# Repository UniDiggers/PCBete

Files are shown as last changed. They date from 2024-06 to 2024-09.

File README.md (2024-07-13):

# PCBete

Création d'un PCB pour la robotique.

## Objectif :

Carte électronique ESP32-S3-WROOM-U1 permettant de controller : 
- Jusqu'à 3 NEMA 17 
- 3 Capteurs TOF VL53L0X (i2c)
- 1 écran OLED 0.96 128*64 (i2c) 
- Buzzer
- LiDAR*

Alimentation via PowerBank 5Ah avec 5V/3A vers la carte en Type-C vers Type-C .

## Consommation théorique 

**3000mA** sont disponibles :

- 1x ESP32 environ **150mA**
- 3x NEMA 17 environ **2400mA**
- 3x TOF VL53L0X environ **60mA**
- 1x Ecran OLED environ **15mA**
- 1x Buzzer environ **10mA**

**TOTAL THEORIQUE : 2635mA / 87%**
*Ce calcul ne prend pas en compte la consommation théorique des composants soudés à la carte.

*le LiDAR est un accessoire optionnel qui peut être ajouté si la consommation instantanée le permet.
1x LiDAR environ **150mA**.

TOTAL THEORIQUE avec LiDAR : **2785mA / 92%**

## Temps d'utilisation théorique

Energie Batterie = Capacité (Ah) x Tension sortie ( Volt).
Energie Batterie = 5Ah x 5 = **25Wh**.

Puissance carte = Intensité (A) x Tension (Volt).
Puissance carte = 3A x 5V = **15W**.

Temps d'utilisation (heure) = Energie Batterie (watt-heures) / Puissance carte (W).
Temps d'utilisation (heure) = 25Wh / 15W = **1.67 heures**.

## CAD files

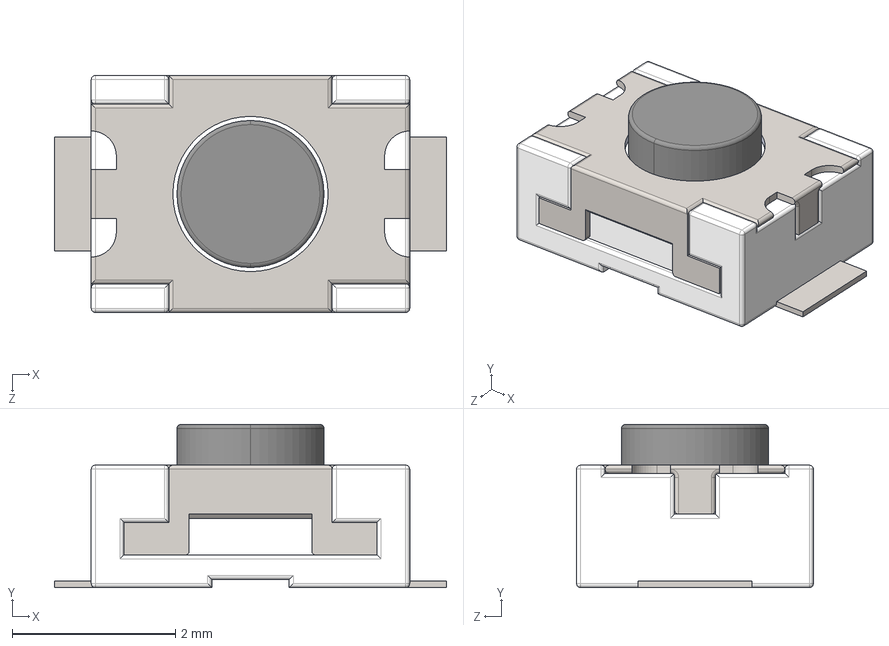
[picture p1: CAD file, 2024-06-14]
3D/Bouton/SKRKAEE020.stp
4.80 x 2.00 x 2.90 mm

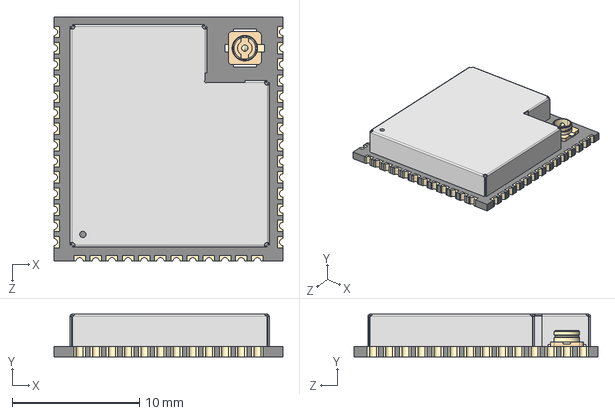
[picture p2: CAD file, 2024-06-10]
3D/ESP32-S3-WROOM-1U/ESP32-S3-WROOM-1U--3DModel-STEP-56544.STEP
18.0 x 3.35 x 19.2 mm

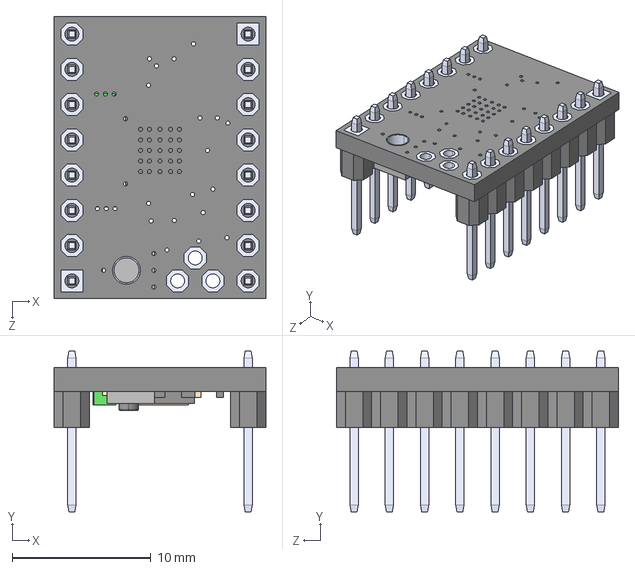
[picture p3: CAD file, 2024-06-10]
3D/TMC2209/TMC2209_SILENTSTEPSTICK.step
15.2 x 11.6 x 20.3 mm

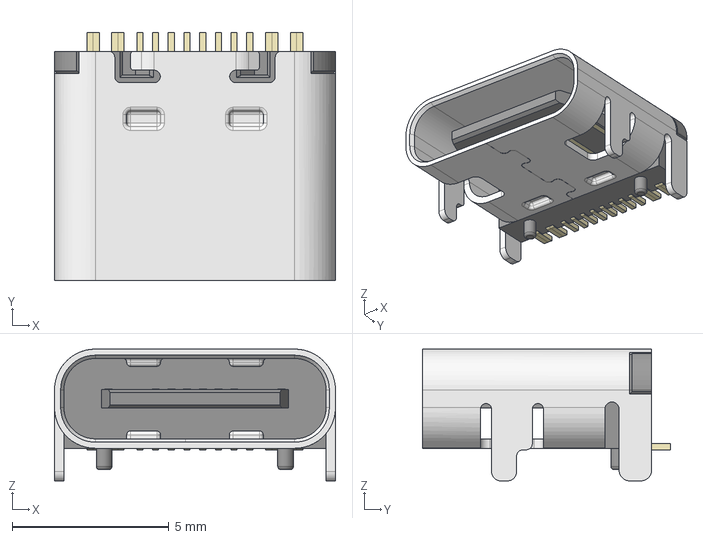
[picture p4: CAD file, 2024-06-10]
3D/USB-Type-C/HRO_TYPE-C-31-M-12.step
8.95 x 7.90 x 4.20 mm

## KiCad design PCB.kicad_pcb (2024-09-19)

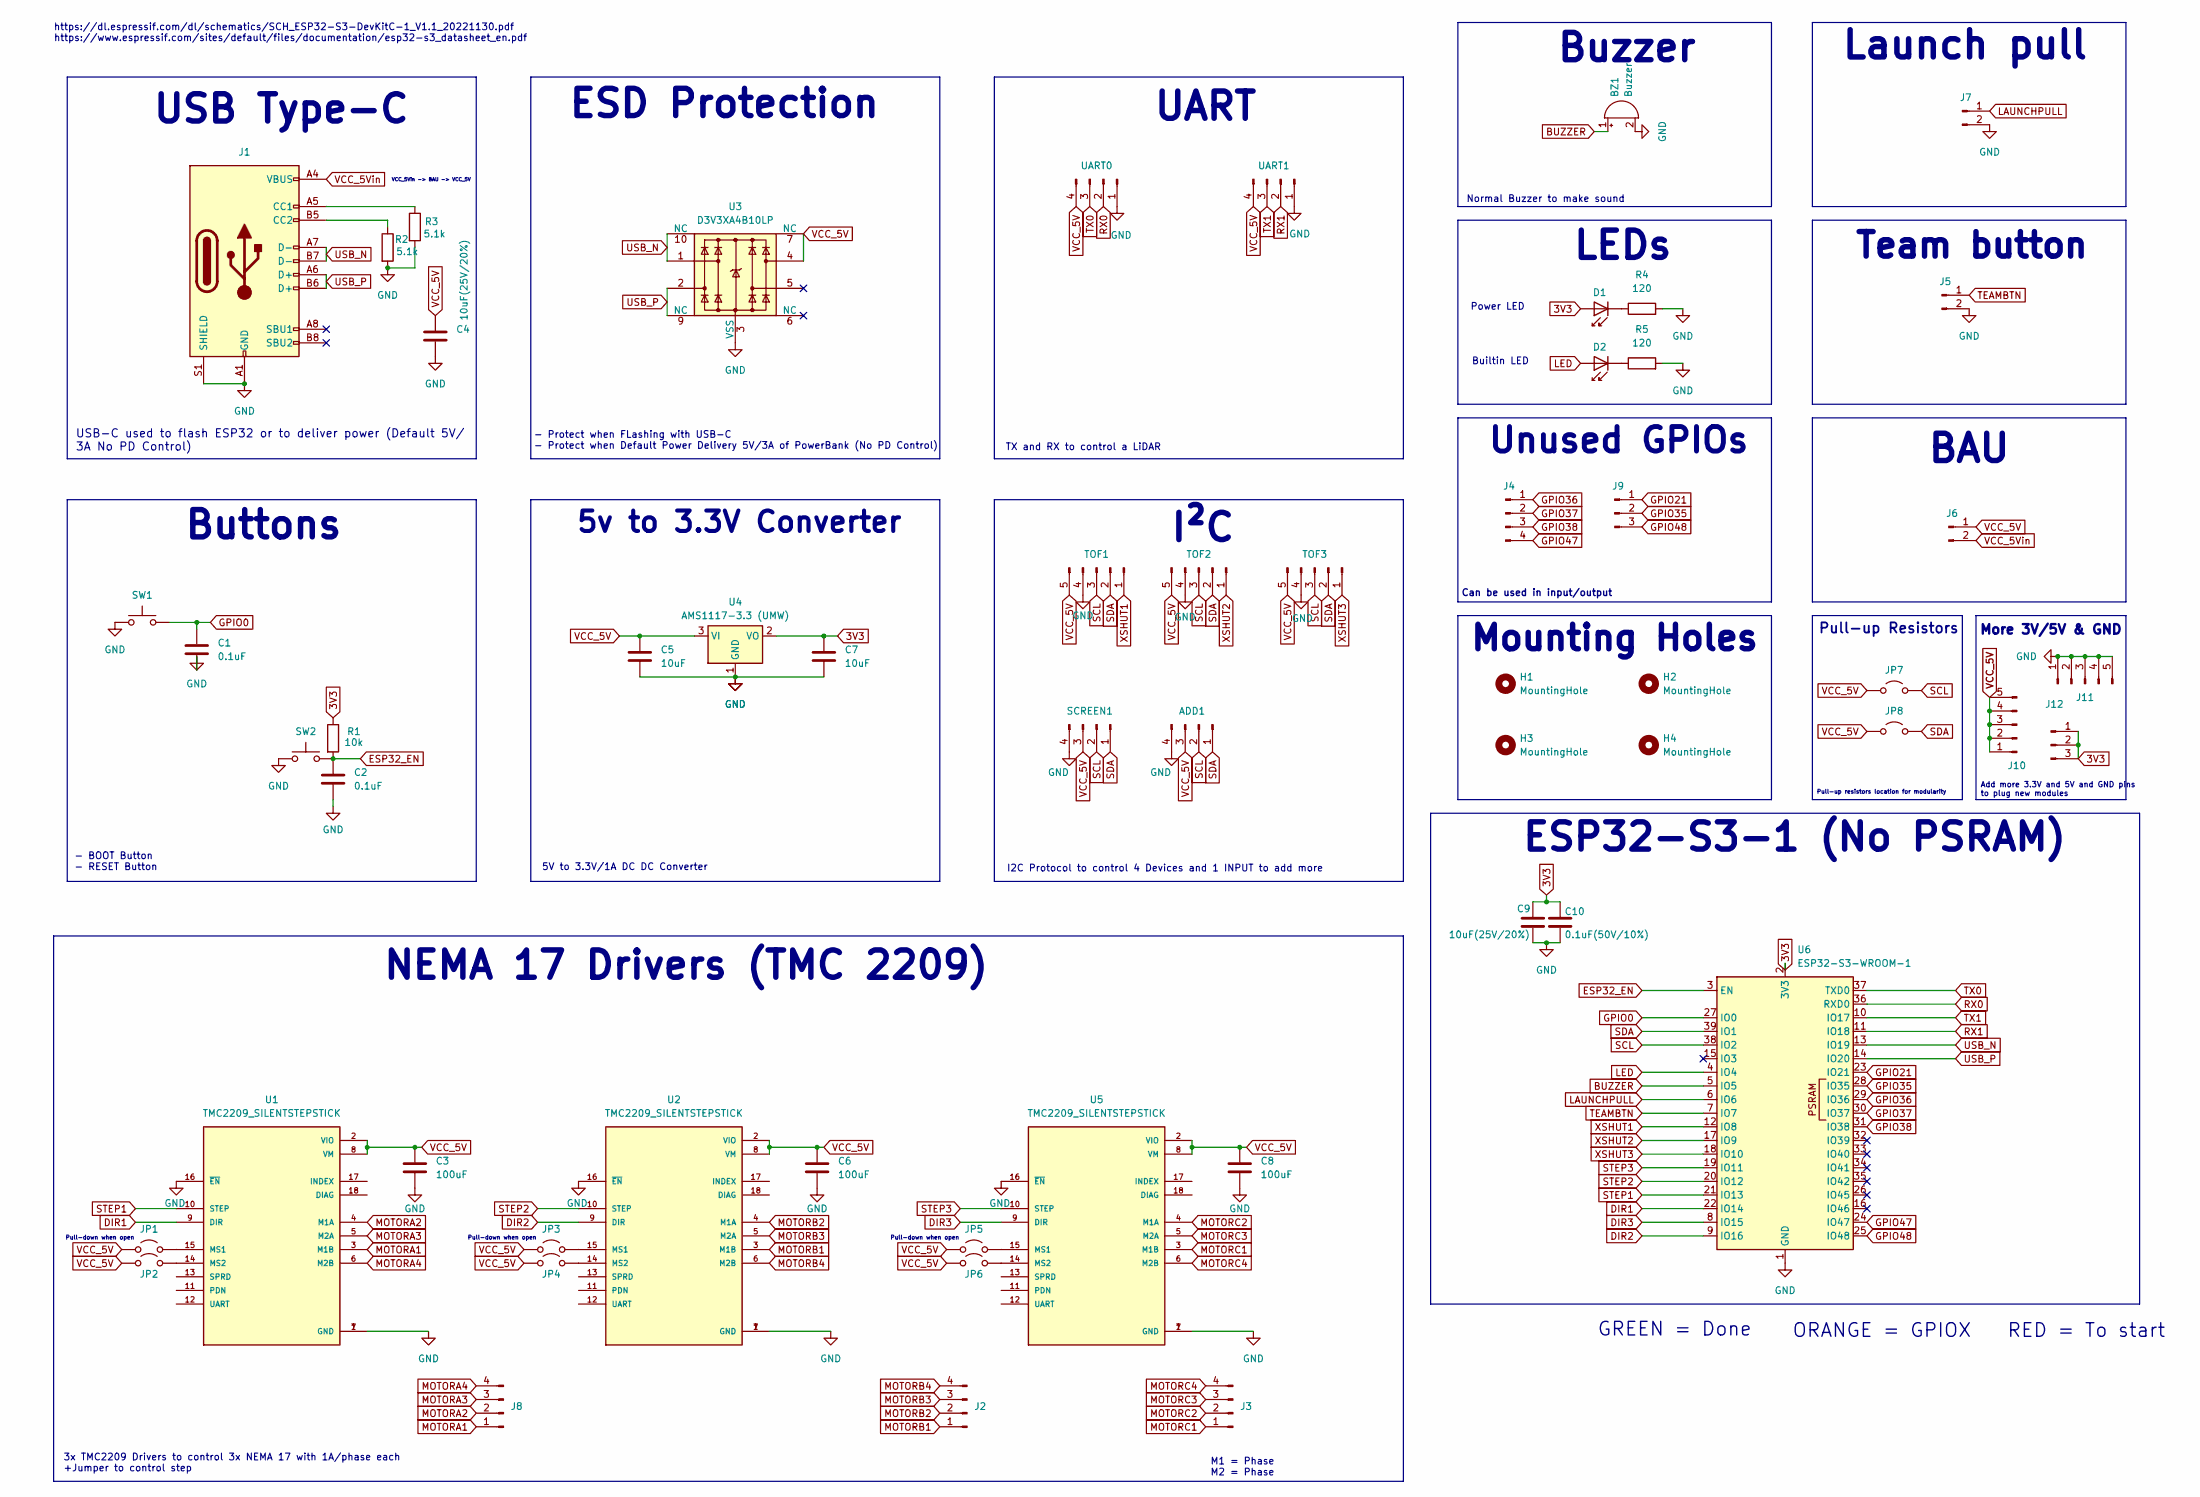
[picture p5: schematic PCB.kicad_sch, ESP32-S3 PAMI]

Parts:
ADD1: Conn_01x04_Pin; PinHeader_1x04_P2.54mm_Vertical
BZ1: Buzzer; Buzzer_12x9.5RM7.6
C1, C2: 0.1uF; R_01005_0402Metric
C3, C6, C8: 100uF; CP_Radial_D10.0mm_P5.00mm
C4, C9: 10uF(25V/20%); R_01005_0402Metric
C5: 10uF; C_1206_3216Metric_Pad1.33x1.80mm_HandSolder
C7: 10uF; R_0603_1608Metric
C10: 0.1uF(50V/10%); R_01005_0402Metric
D1, D2: LED_0603_1608Metric
H1, H2, H3, H4: MountingHole; MountingHole_3.2mm_M3
J1: USB_C_Receptacle_USB2.0_16P; USB_C_Receptacle_HRO_TYPE-C-31-M-12
J2, J3, J8: Conn_01x04_Pin; PinHeader_1x04_P2.54mm_Vertical
J4: Conn_01x07_Pin; PinHeader_1x04_P2.54mm_Vertical
J5, J6, J7: Conn_01x02_Pin; PinHeader_1x02_P2.54mm_Vertical
J9: Conn_01x07_Pin; PinHeader_1x03_P2.54mm_Vertical
J10, J11: Conn_01x05_Pin; PinHeader_1x05_P2.54mm_Vertical
J12: Conn_01x03_Pin; PinHeader_1x03_P2.54mm_Vertical
JP1, JP2, JP3, JP4, JP5, JP6: Jumper_2_Open; PinHeader_1x02_P2.54mm_Vertical
JP7, JP8: Jumper_2_Open; R_1206_3216Metric_Pad1.30x1.75mm_HandSolder
R1: 10k; R_01005_0402Metric
R2, R3: 5.1k; R_0805_2012Metric_Pad1.20x1.40mm_HandSolder
R4, R5: 120; R_01005_0402Metric
SCREEN1: Conn_01x04_Pin; PinHeader_1x04_P2.54mm_Vertical
SW1, SW2: SW_Push; SW_Push_SPST_NO_Alps_SKRK
TOF1, TOF2, TOF3: Conn_01x05_Pin; PinHeader_1x05_P2.54mm_Vertical
U1, U2, U5: TMC2209_SILENTSTEPSTICK; MODULE_TMC2209_SILENTSTEPSTICK; PARTREV 1.20
U3: D3V3XA4B10LP; Diodes_UDFN-10_1.0x2.5mm_P0.5mm
U4: AMS1117-3.3 (UMW); SOT-223-3_TabPin2
U6: ESP32-S3-WROOM-1; ESP32-S3-WROOM-1U
UART0, UART1: Conn_01x04_Pin; PinHeader_1x04_P2.54mm_Vertical

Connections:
3V3: C7.1, C9.1, C10.1, D1.2 (A), J12.1, J12.2, J12.3, R1.1, U4.2 (VO), U6.2 (3V3)
BUZZER: BZ1.1 (+), U6.5 (IO5)
DIR1: U1.9 (DIR), U6.22 (IO14)
DIR2: U2.9 (DIR), U6.9 (IO16)
DIR3: U5.9 (DIR), U6.8 (IO15)
ESP32_EN: C2.1, R1.2, SW2.2, U6.3 (EN)
GND: ADD1.4, BZ1.2 (-), C1.2, C2.2, C3.2, C4.2, C5.2, C6.2, C7.2, C8.2, C9.2, C10.2, J1.A1 (GND), J1.A12 (GND), J1.B1 (GND), J1.B12 (GND), J1.S1 (SHIELD), J5.2, J7.2, J11.1, J11.2, J11.3, J11.4, J11.5, R2.2, R3.2, R4.2, R5.2, SCREEN1.4, SW1.1, SW2.1, TOF1.4, TOF2.4, TOF3.4, U1.1 (GND), U1.7 (GND), U1.16 (~EN), U2.1 (GND), U2.7 (GND), U2.16 (~EN), U3.3 (VSS), U3.8 (VSS), U4.1 (GND), U5.1 (GND), U5.7 (GND), U5.16 (~EN), U6.1 (GND), U6.40 (GND), U6.41 (GND), UART0.1, UART1.1; also elsewhere on the board
GPIO0: C1.1, SW1.2, U6.27 (IO0)
GPIO21: J9.1, U6.23 (IO21)
GPIO35: J9.2, U6.28 (IO35)
GPIO36: J4.1, U6.29 (IO36)
GPIO37: J4.2, U6.30 (IO37)
GPIO38: J4.3, U6.31 (IO38)
GPIO47: J4.4, U6.24 (IO47)
GPIO48: J9.3, U6.25 (IO48)
LAUNCHPULL: J7.1, U6.6 (IO6)
LED: D2.2 (A), U6.4 (IO4)
MOTORA1: J8.1, U1.3 (M1B)
MOTORA2: J8.2, U1.4 (M1A)
MOTORA3: J8.3, U1.5 (M2A)
MOTORA4: J8.4, U1.6 (M2B)
MOTORB1: J2.1, U2.3 (M1B)
MOTORB2: J2.2, U2.4 (M1A)
MOTORB3: J2.3, U2.5 (M2A)
MOTORB4: J2.4, U2.6 (M2B)
MOTORC1: J3.1, U5.3 (M1B)
MOTORC2: J3.2, U5.4 (M1A)
MOTORC3: J3.3, U5.5 (M2A)
MOTORC4: J3.4, U5.6 (M2B)
unnamed: D1.1 (K), R4.1
unnamed: D2.1 (K), R5.1
unnamed: J1.A5 (CC1), R3.1
unnamed: J1.B5 (CC2), R2.1
unnamed: JP1.2 (B), U1.15 (MS1)
unnamed: JP2.2 (B), U1.14 (MS2)
unnamed: JP3.2 (B), U2.15 (MS1)
unnamed: JP4.2 (B), U2.14 (MS2)
unnamed: JP5.2 (B), U5.15 (MS1)
unnamed: JP6.2 (B), U5.14 (MS2)
RX0: U6.36 (RXD0), UART0.2
RX1: U6.11 (IO18), UART1.2
SCL: ADD1.2, JP7.2 (B), SCREEN1.2, TOF1.3, TOF2.3, TOF3.3, U6.38 (IO2); also elsewhere on the board
SDA: ADD1.1, JP8.2 (B), SCREEN1.1, TOF1.2, TOF2.2, TOF3.2, U6.39 (IO1); also elsewhere on the board
STEP1: U1.10 (STEP), U6.21 (IO13)
STEP2: U2.10 (STEP), U6.20 (IO12)
STEP3: U5.10 (STEP), U6.19 (IO11)
TEAMBTN: J5.1, U6.7 (IO7)
TX0: U6.37 (TXD0), UART0.3
TX1: U6.10 (IO17), UART1.3
USB_N: J1.A7 (D-), J1.B7 (D-), U3.1, U3.10 (NC), U6.13 (IO19)
USB_P: J1.A6 (D+), J1.B6 (D+), U3.2, U3.9 (NC), U6.14 (IO20)
VCC_5V: ADD1.3, C3.1, C4.1, C5.1, C6.1, C8.1, J6.1, J10.1, J10.2, J10.3, J10.4, J10.5, JP1.1 (A), JP2.1 (A), JP3.1 (A), JP4.1 (A), JP5.1 (A), JP6.1 (A), JP7.1 (A), JP8.1 (A), SCREEN1.3, TOF1.5, TOF2.5, TOF3.5, U1.2 (VIO), U1.8 (VM), U2.2 (VIO), U2.8 (VM), U3.4, U3.7 (NC), U4.3 (VI), U5.2 (VIO), U5.8 (VM), UART0.4, UART1.4; also elsewhere on the board
VCC_5Vin: J1.A4 (VBUS), J1.A9 (VBUS), J1.B4 (VBUS), J1.B9 (VBUS), J6.2
XSHUT1: TOF1.1, U6.12 (IO8)
XSHUT2: TOF2.1, U6.17 (IO9)
XSHUT3: TOF3.1, U6.18 (IO10)

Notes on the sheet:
USB-C used to flash ESP32 or to deliver power (Default 5V/ 3A No PD Control)
Pull-up Resistors
Normal Buzzer to make sound
3x TMC2209 Drivers to control 3x NEMA 17 with 1A/phase each +Jumper to control step
Pull-down when open
Unused GPIOs
Buttons
GREEN = Done
ESP32-S3-1 (No PSRAM)
Can be used in input/output
RED = To start
BAU
Pull-down when open
USB Type-C
5v to 3.3V Converter
Buzzer
5V to 3.3V/1A DC DC Converter
https://www.espressif.com/sites/default/files/documentation/esp32-s3_datasheet_en.pdf
Power LED
ESD Protection
Mounting Holes
I²C
Add more 3.3V and 5V and GND pins to plug new modules
TX and RX to control a LiDAR
Pull-up resistors location for modularity
VCC_5Vin -> BAU -> VCC_5V
Team button
ORANGE = GPIOX
Builtin LED
NEMA 17 Drivers (TMC 2209)
UART
I2C Protocol to control 4 Devices and 1 INPUT to add more
https://dl.espressif.com/dl/schematics/SCH_ESP32-S3-DevKitC-1_V1.1_20221130.pdf
More 3V/5V & GND
Launch pull
M1 = Phase M2 = Phase
- BOOT Button - RESET Button
LEDs
- Protect when FLashing with USB-C - Protect when Default Power Delivery 5V/3A of PowerBank (No PD Control)

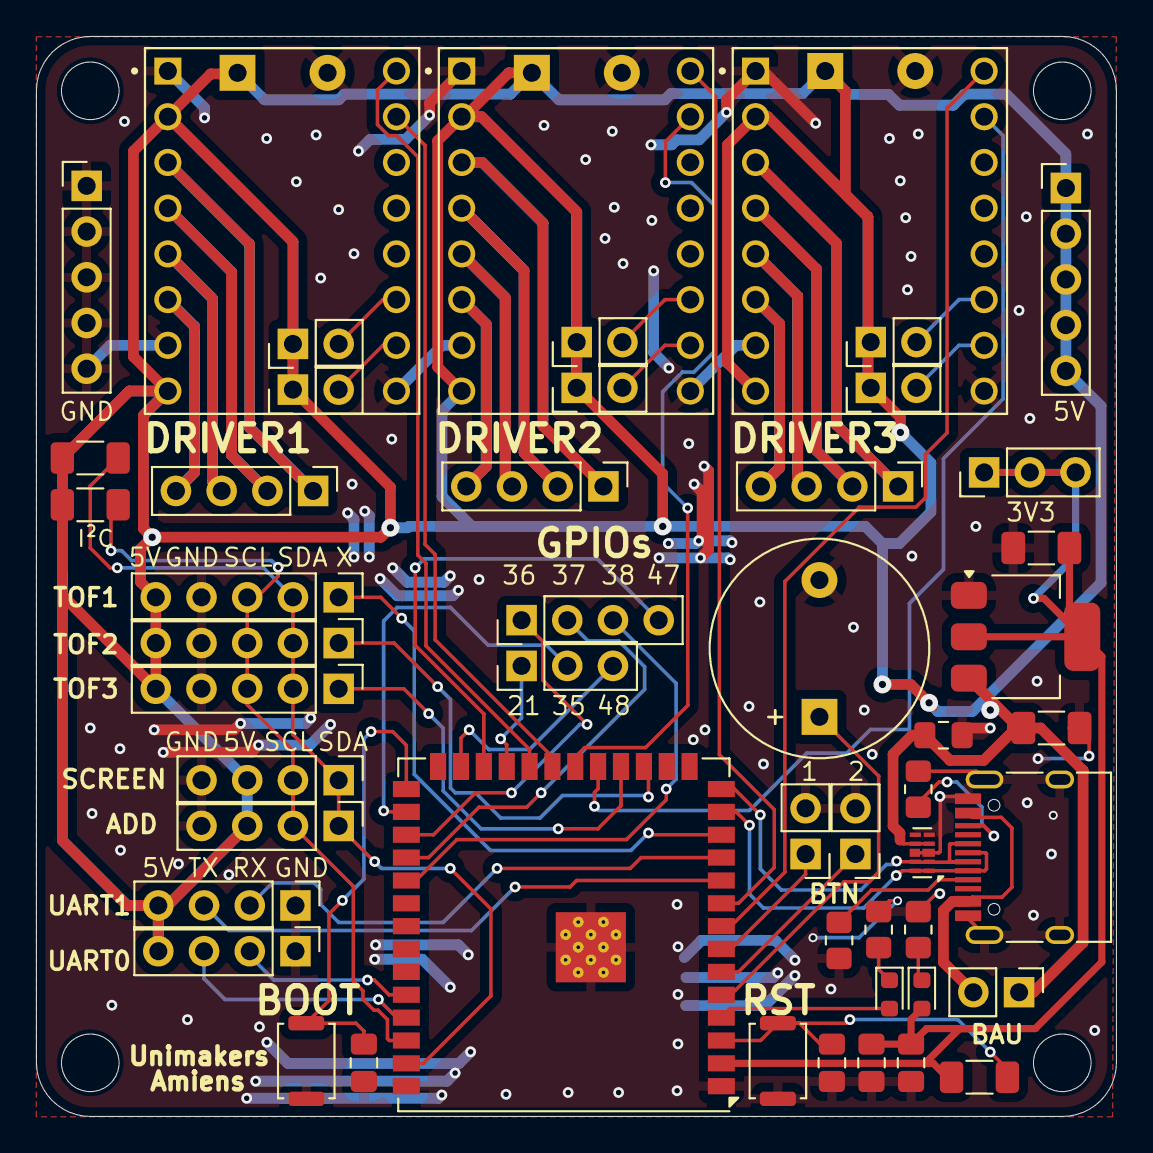
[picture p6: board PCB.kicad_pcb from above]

Board: 2 copper layers, 60.0 x 60.0 mm, 57 parts (0 on the bottom side), 56 nets.

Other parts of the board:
ADD: Conn_01x04_Pin; PinHeader_1x04_P2.54mm_Vertical
SCREEN: Conn_01x04_Pin; PinHeader_1x04_P2.54mm_Vertical

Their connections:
GND: ADD.4, SCREEN.4; also elsewhere on the board
SCL: ADD.2, SCREEN.2; also elsewhere on the board
SDA: ADD.1, SCREEN.1; also elsewhere on the board
VCC_5V: ADD.3, SCREEN.3; also elsewhere on the board

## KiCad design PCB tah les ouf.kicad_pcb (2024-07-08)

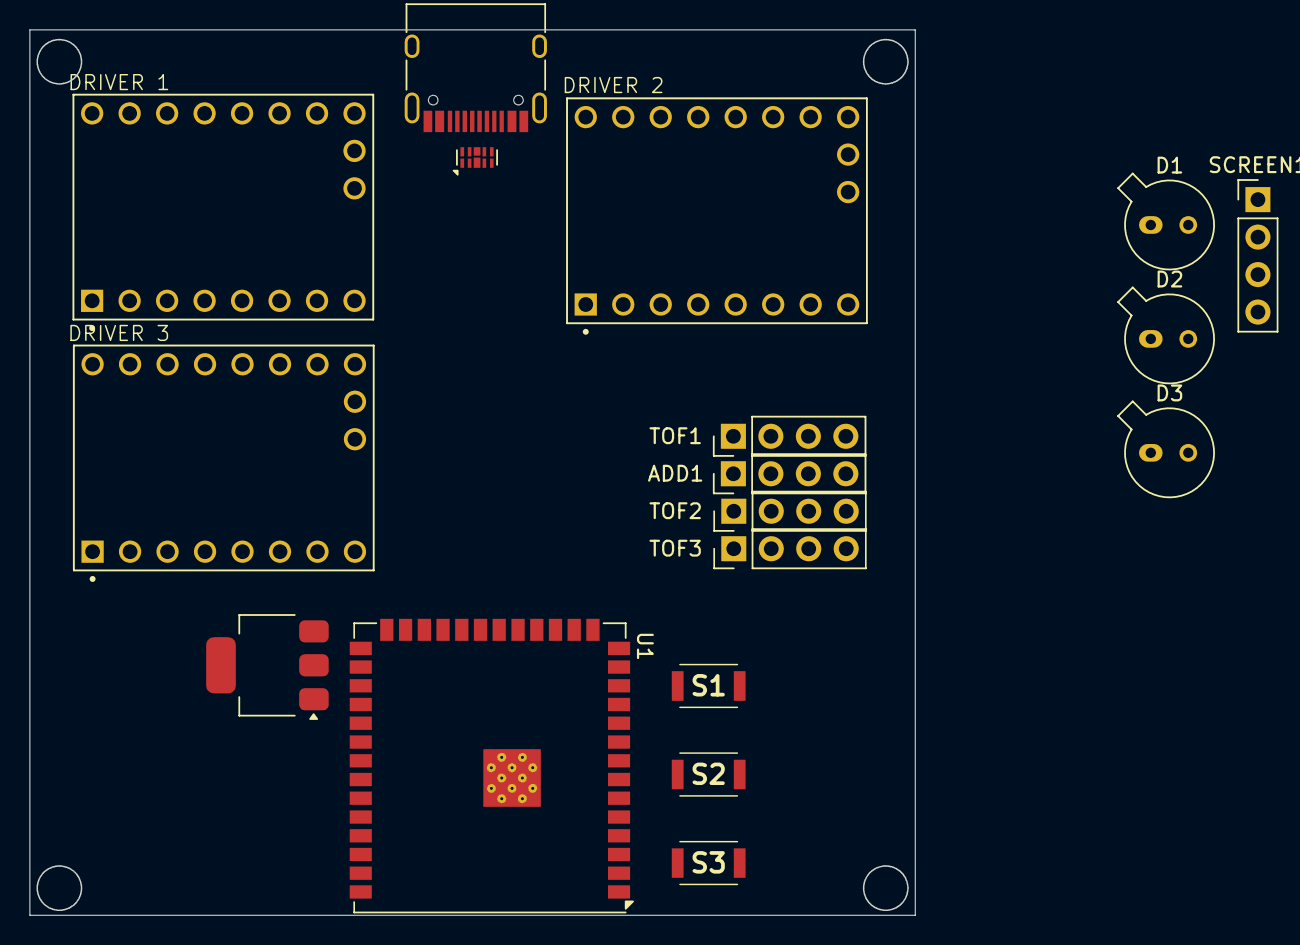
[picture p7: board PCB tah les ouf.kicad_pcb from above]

Board: 2 copper layers, 60.0 x 60.0 mm, 18 parts (0 on the bottom side), 9 nets, no tracks yet.

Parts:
ADD1: Conn_01x04_Pin; PinHeader_1x04_P2.54mm_Vertical
D1, D2, D3: TO-18-2_Window
J1: USB_C_Receptacle_USB2.0_16P; USB_C_Receptacle_HRO_TYPE-C-31-M-12
S1: BOOT; SKRKAEE020
S2: RST; SKRKAEE020
S3: BUILTIN; SKRKAEE020
SCREEN1: Conn_01x04_Pin; PinHeader_1x04_P2.54mm_Vertical
TOF1, TOF2, TOF3: Conn_01x04_Pin; PinHeader_1x04_P2.54mm_Vertical
U1: ESP32-S3-WROOM-1; ESP32-S3-WROOM-1U
U2, U3, U4: TMC2209_SILENTSTEPSTICK; MODULE_TMC2209_SILENTSTEPSTICK
U6: D3V3XA4B10LP; Diodes_UDFN-10_1.0x2.5mm_P0.5mm
U7: AMS1117-3.3 (UMW); SOT-223-3_TabPin2

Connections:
/3V3: U1.2 (3V3), U7.2 (VO)
/ESP32_EN: S2.2, U1.3 (EN)
/GPIO0: S1.2, U1.27 (IO0)
/USB_N: J1.A7 (D-), J1.B7 (D-), U1.13 (IO19), U6.1, U6.10 (NC)
/USB_P: J1.A6 (D+), J1.B6 (D+), U1.14 (IO20), U6.2, U6.9 (NC)
GND: ADD1.4, J1.A1 (GND), J1.A12 (GND), J1.B1 (GND), J1.B12 (GND), J1.S1 (SHIELD), S1.1, S2.1, S3.1, SCREEN1.4, TOF1.4, TOF2.4, TOF3.4, U1.1 (GND), U1.40 (GND), U1.41 (GND), U2.1 (GND), U2.7 (GND), U3.1 (GND), U3.7 (GND), U4.1 (GND), U4.7 (GND), U6.3 (VSS), U6.8 (VSS), U7.1 (GND)
SCL: ADD1.2, SCREEN1.2, TOF1.2, TOF2.2, TOF3.2, U1.11 (IO18)
SDA: ADD1.1, SCREEN1.1, TOF1.1, TOF2.1, TOF3.1, U1.10 (IO17)
VCC_5V: ADD1.3, D1.2 (A), D2.2 (A), D3.2 (A), J1.A4 (VBUS), J1.A9 (VBUS), J1.B4 (VBUS), J1.B9 (VBUS), SCREEN1.3, TOF1.3, TOF2.3, TOF3.3, U6.4, U6.7 (NC), U7.3 (VI)

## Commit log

2024-06-10 init commit
    [HRO_TYPE-C-31-M-12.step, PCB tah les ouf.kicad_pcb, PCB tah les ouf.kicad_sch]
2024-06-10 Ajout variables de chemin
    [PCB tah les ouf.kicad_pcb]
2024-06-10 Ajout ESP32-S3-WROOM-1U
    [ESP32-S3-WROOM-1U--3DModel-STEP-56544.STEP, PCB tah les ouf.kicad_pcb]
2024-06-10 Ajustement TMC
    [PCB tah les ouf.kicad_pcb, PCB tah les ouf.kicad_sch]
2024-06-10 AJOUT driver stepper
    [PCB tah les ouf.kicad_pcb, PCB tah les ouf.kicad_sch, TMC2209_SILENTSTEPSTICK.step]
2024-06-11 Fix problem / ESD Protection
    [PCB tah les ouf.kicad_pcb, PCB tah les ouf.kicad_sch]
2024-06-11 correction problemes
    [PCB tah les ouf.kicad_pcb, PCB tah les ouf.kicad_sch]
2024-06-11 Ajout Auto flash mode
    [PCB tah les ouf.kicad_pcb, PCB tah les ouf.kicad_sch]
2024-06-11 auto flash mode v2
    [PCB tah les ouf.kicad_pcb, PCB tah les ouf.kicad_sch]
2024-06-14 Ajout switches DIP drivers & 5 to 3.3 converter
    [PCB tah les ouf.kicad_sch]
2024-06-14 Fix 5 to 3.3 converter
    [PCB tah les ouf.kicad_sch]
2024-06-14 ajout boutons rst,boot,builtin
    [SKRKAEE020.stp]
2024-06-14 Add buttons for reset, boot, and built-in functions
    [PCB tah les ouf.kicad_pcb, PCB tah les ouf.kicad_sch]
2024-07-08 Suppression TMC2209 x1
    [PCB tah les ouf.kicad_pcb, PCB tah les ouf.kicad_sch]
2024-07-10 Correction label + terminé i2c/uart
    [PCB tah les ouf.kicad_sch]
2024-07-13 Ajout MD et correction erreurs
    [PCB.kicad_pcb, PCB.kicad_sch]
2024-09-13 Ajout empreintes
    [PCB.kicad_pcb, PCB.kicad_sch]
2024-09-13 Fix court-circuit
    [PCB.kicad_sch]
2024-09-13 Correction bug schématic
    [PCB.kicad_pcb, PCB.kicad_sch]
2024-09-14 routage terminé
    [PCB.kicad_pcb, PCB.kicad_sch]
2024-09-15 chnagement jumper + orga
    [PCB.kicad_pcb, PCB.kicad_sch]
2024-09-15 ajout plus de 5V et GND
    [PCB.kicad_pcb, PCB.kicad_sch]
2024-09-16 Test DRC + corrections
    [PCB.kicad_pcb]
2024-09-16 ajout hub 3.3v
    [PCB.kicad_pcb, PCB.kicad_sch]
2024-09-16 Dernier DRC après modicifications
    [PCB.kicad_pcb, PCB.kicad_sch]
2024-09-17 ajout plan de masse
    [PCB-B_Cu.gbr, PCB-B_Mask.gbr, PCB-B_Paste.gbr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]
2024-09-17 ajout trous de montage
    [PCB.kicad_pcb]
2024-09-17 BOM à réaliser
    [PCB-B_Cu.gbr, PCB-B_Mask.gbr, PCB-B_Paste.gbr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]
2024-09-19 Test DRC OK
    [PCB.csv, PCB.kicad_pcb, PCB.kicad_sch]
